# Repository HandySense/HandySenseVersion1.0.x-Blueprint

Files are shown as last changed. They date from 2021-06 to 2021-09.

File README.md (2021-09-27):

hds-logo_0
- 📫 VDO สอนใช้งาน HandySense: ...
[VDO_สอนใช้งาน_HandySense_Link_(คลิกเพื่อดู)](https://www.youtube.com/watch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) 

# HandySense Board 
 

* HandySense คือ ระบบอุปกรณ์ IOT สำหรับเกษตรอัจฉริยะที่สามารถแสดงค่าข้อมูล ปัจจัยในการควบคุมผลผลิตทางการเกษตร โดยใช้เทคโนโลยีเซนเซอร์เข้ามาช่วยในกระบวนการเพาะปลูกซึ่งช่วยให้เกษตรกรสามารถควบคุมสภาวะแวดล้อมในการปลูกได้ตั้งแต่เริ่มต้นส่งผลให้สามารถควบคุมคุณภาพและประเมินปริมาณผลผลิต 
* รวมถึงช่วยเรื่องการเพิ่มคุณค่าของผลผลิตได้โดยใช้การควบคุมกระบวนการเพาะปลูกเพื่อให้ผลผลิตออกในช่วงที่มีความต้องการหรือผลผลิตขาดแคลนรวมถึงการช่วยเกษตรกรนำองค์ความรู้ที่เกิดจากทักษะที่ไม่สามารถถ่ายทอดให้เข้าใจได้เนื่องจากเป็นภูมิปัญญาและเป็นการทำเกษตรกรรมแบบวิถีชาวบ้านโดยการลองผิดลองถูกหรือเป็นองค์ความรู้ที่สืบทอดต่อกัน
 
สารบัญ (Table of contents)
=========================

<!--ts-->
   * [Descriptions](#descriptions)
     องค์ประกอบของบอร์ด HandySense 
   * [Schematic](#schematic)
     ไฟล์ .brd (PCB  layout) และ .sch
   * [Blueprint](#blueprint)
     (GerberFile)
   * [BOM](#bom)
     รายการอุปกรณ์อิเล็กทรอนิกส์ BOM (bill of material)
   * [Manual](#manual)
     คู่มือการใช้งาน 
<!--te-->

Descriptions
===========
### องค์ประกอบของบอร์ด-HandySense 

โดย HandySense Board ประกอบด้วยอินเตอร์เฟสการสื่อสารหลักเป็น I2C, SPI, Analog, WIFI 
* I2C ต่อ Connector ออกมาให้ใช้งาน 2 ชุด (+5V)  
* Analog ต่อ Connector ออกมาให้ใช้งาน 3 pin ได้แก่ IO36(A0), IO39(A3), IO32(A4)
* SPI ขา CS/SS เป็น IO5 บนบอร์ดไม่ได้ต่ออุปกรณ์ แต่ต่อกับ IDC10 (block 10 pin) 
* ส่วน WIFI สื่อสารข้อมูลกับ Server เป็นหลัก
* Output เป็น Relay 220V AC 10A โดยต่อ pin ได้แก่ IO25, IO4, IO12, IO13 

* รายละเอียดแสดงดังภาพ (*แสดงพอสังเขป โดยรายละเอียดอ่านคู่มือเพิ่มเติม)

hds-pinio

Schematic
===========
### ไฟล์ .brd (PCB  layout) และ .sch
สำหรับ HandySense version นี้ออกแบบด้วยโปรแกรม Autodesk Eagle ซึ่งไฟล์สามารถกดดาวน์โหลดได้ด้านบน 

* ไฟล์ .brd (PCB  layout) และ .sch
sch

Blueprint
===========
### Gerber File
สำหรับ BluePrint จะ save เป็น Gerber File ที่สามารถนำไปสั่งผลิตได้ โดยไม่ต้องปรับแก้อะไร สามารถดาวน์โหลดได้ด้านบน

* Gerber File 
gerber

BOM
===========
### รายการอุปกรณ์อิเล็กทรอนิกส์ BOM (Bill Of Material)
* สำหรับรายการอุปกรณ์อิเล็กทรอนิกส์ของบอร์ด HandySense มีรายการทั้งหมดอยู่ในไฟล์ ชื่อ HandySense_v1.0.2_BOM.ods (เปิดดูด้วยโปรแกรม MS Excel)
ซึ่งจะบอกรายละเอียดที่จำเป็นและราคาต่อบอร์ดหรือราคารวมคร่าว ๆ ได้ (อาจจะมี +,- เนื่องจากราคามีการอับเดตเป็นช่วง ๆ ขึ้นอยู่กับผู้ขาย) สามารถที่จะระบุจำนวนบอร์ดที่ต้องการได้ในช่อง

* BOM (Bill Of Material)
bom

Manual
===========
### คู่มือการใช้งาน 
* สำหรับคู่มือการใช้งาน จะประกอบไปด้วย 2 เล่ม ได้แก่ 
* คู่มือสอนใช้งานบอร์ด HandySense
* คู่มือสอนใช้งาน HandySense Dashboard 

bom

# Open Hardware Facts
ost

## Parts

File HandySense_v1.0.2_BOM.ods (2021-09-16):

Handy Sense version 1.0.2
คำอธิบาย : - Product P/N คือหมายเลขที่สามารถนำไปสั่งซื้อผ่านทางร้านได้โดยตรงและง่ายขึ้น - Unit/Board แสดงจำนวนอุปกรณ์ต่อ 1 บอร์ด - Unit/Boards แสดงจำนวอุปกรณ์ต่อจำนวนบอร์ดที่ต้องการผลิต
จำนวนบอร์ดที่ต้องการผลิต |  | 10 | บอร์ด
 |  | * หมายเหตุ ระบุจำนวนที่ต้องการผลิตในช่อง
Part | Value | Device | Package | Product P/N: | ES P/N: | Unit/Board | Unit/Boards | Vendor | ของเหลือ | ซื้อเพิ่ม | ราคา/หน่วย | ราคาต่อ/จำนวนบอร์ดที่ต้องการ
C1,C2,C4 | 10uF | 10UF-16V-10%(TANT) | EIA3216 | TCA1C106M8R | 0176-0142-4 | 3 | 30 | ES | 14 | 16 | 2.5 | 40.00
C6 | 100uF | CAP_POL7343 | EIA7343 | TAJD107K016RNJ | 0092-0305-6 | 1 | 10 | ES | 5 | 5 | 12.86 | 64.30
C3,5,7-12 | 0.1uF | CAP0805 | 805 | CL21B104KBCNNNC | 0082-0192-3 | 5 | 50 | ES | 50 | 0 | 0.42 | 0.00
D1,D2,D3 |  | DIODE-SCHOTTKY-MBRA140 | SMA-DIODE | RB168L-40TE25 | 0176-0726-8 | 3 | 30 | ES | 3 | 27 | 2.79 | 75.33
Ju1 | Female Header | Female Header 6 Pins,Single Row | FHSS06G10 | - | 0007-1218-3 | 1 | 10 | ES | 5 | 5 | 4.31 | 21.55
USB | MICRO_USB_B_HIROSE_ZX62-B-5PA(11) | MICRO_USB_B_HIROSE_ZX62-B-5PA(11) | USB_MICRO_B-HIROSE-ZX62-B-5PA(11) | MRUMRB05FTKTY-30U | 0007-1315-9 | 1 | 10 | ES | 0 | 10 | 20.65 | 206.50
K1-4 | JS-M1-9V-4 | JS-M1-9V-4 | JS-M | HRS4H-S-DC5V-C | 0181-0027-9 | 4 | 40 | ES | 0 | 40 | 19.71 | 788.40
LED1,2 | BLUE | LEDCHIPLED_BLUE | CHIPLED_0805 | TO-2013BC-BF | 0010-1475-9 | 1 | 10 | ES | 14 | 0 | 2.26 | 0.00
LED9,11,13,15 | Green | LEDCHIPLED_GREEN | CHIPLED_0805 | TO-2013BC-MGE | 0010-0326-9 | 4 | 40 | ES | 0 | 40 | 1.54 | 61.60
LED3 | RED | LEDCHIPLED_RED | CHIPLED_0805 | TO-2013BC-MRE | 0010-0327-2 | 2 | 20 | ES | 20 | 0 | 1.54 | 0.00
LED7 | Yellow | LEDCHIPLED_YELLOW | CHIPLED_0805 | TO-2013BC-MYE | 0010-1457-5 | 1 | 10 | ES | 12 | 0 | 1.31 | 0.00
OK1-4 | PC817 | PC817 | DIL04 | PC817X3NSZ9F | 0084-0059-3 | 4 | 40 | ES | 40 | 0 | 3.16 | 0.00
Q1-6 | MMBT2222A | TRANSISTOR_NPNMMBT2222A | SOT23-3 | MMBT2222ALT1G | 0235-0237-0 | 6 | 60 | ES | 0 | 60 | 0.74 | 44.40
R1-4,7,8,14,16,19,22,25,39-50 | 10k | R-US_R0805 | R0805 | MCR10ERTJ103 | 0176-0924-2 | 8 | 80 | ES | 0 | 80 | 0.15 | 12.00
R5,6,9,10,15,17-21,23-26 | 1k | R-US_R0805 | R0805 | MCR10EZPJ102 | 0176-1715-9 | 16 | 160 | ES | 0 | 160 | 0.15 | 24.00
SW0,SW1,SW2 | TACTILE-SWITCH-PTH | TACTILE-SWITCH-PTH | TAC-SWITCH-PTH | TC-0104-X-ROHS | 0171-0104-9 | 3 | 30 | ES | 0 | 30 | 1.49 | 44.70
LDO | LDO Voltage Regulator,3.3V | V_REG_LM1117SOT223 | SOT223 | LM1117MPX-3.3/NOPB | 0078-0169-8 | 1 | 10 | ES | 0 | 10 | 15.11 | 151.10
X1 | ESP-32 | ESP-32 | ESP-32 | ESP32-WROOM-32 | 1082-0002-1 | 1 | 10 | ES | 0 | 10 | 130.5 | 1,305.00
X7,10 | Screw Terminal Block 4Pins,Pitch 5.00mm | W237-04P | W237-4P | ED500V-04P | 0005-0111-7 | 3 | 30 | ES | 30 | 0 | 12.95 | 0.00
X2,6,8,12 | Screw Terminal Block 3Pins,Pitch 5.00mm | W237-03P | W237-133 | EK500V-3P | 0005-0067-0 | 4 | 40 | ES | 20 | 20 | 11.02 | 220.40
X4,5,11 | Screw Terminal Block 3Pins,Pitch 5.00mm | - | - | DG126-03P-14-00A(H) | 0330-0049-4 | 3 | 30 | ES | 20 | 10 | 3.28 | 32.80
IDC10 | BOX Header Connector 10 Pins | BOX Header Connector 10 Pins Dual Row Pitch 2.54 mm | PAK100/2500-10 | SCP10GS31/RH | 0007-0455-4 | 1 | 10 | ES | 3 | 7 | 2.88 | 20.16
Q9 | 32.768kHZ | CRYSTALTC26H | TC26H | Q11C02RX1002200 | 0057-0038-2 | 1 | 10 | ES | 0 | 10 | 2.9 | 29.00
U2 | CP2102N-A01-GQFN28 | CP2102N-A01-GQFN28 | QFN50P500X500X80-29N | IC Usb To Uart |  | 1 | 10 | RS | 0 | 10 | 44.02 | 440.20
BT1 | Battery Holder for CR-2025 | BATTERY-20MM_PTH_KIT | BATTCOM_20MM_PTH_KIT | BH-25T-GLD | 0197-0001-3 | 1 | 10 | ES | 5 | 5 | 4.86 | 24.30
BT2 | 3V/225mAh, Diameter 20 mm | Lithium Coin Battery 3V/225mAh, Diameter 20 mm | BATTCOM_20MM_PTH_KIT | CR-2032L/BE | 0102-0020-1 | 1 | 10 | ES | 0 | 10 | 9.28 | 92.80
U3 | DS1307Z | DS1307Z | SO08-0.15 | Maxim DS1307 | 0067-0085-4 | 1 | 10 | ES | 5 | 5 | 21.16 | 105.80
R4 | 47.5k | R-US_R0805 | R0805 | MCR03EZPFX4702 | 0176-2036-4 | 1 | 10 | ES | 30 | 0 | 0.11 | 0.00
R6 | 2k | R-US_R0805 | R0805 | 0805W8F2001T5E | 0150-2037-4 | 1 | 10 | ES | 40 | 0 | 0.1 | 0.00
R22 | 22.1k | Thick Fillm Chip Resistors 1/4W | 223 | MCR18EZHJ223 | 0176-1928-6 | 1 | 10 | ES | 30 | 0 | 0.17 | 0.00
R4.7 | 4.7K |  |  |  | 0150-1882-3 | 3 | 30 | ES | 30 | 0 | 0.11 | 0.00
H1-2 | 2 pin | Water 2 Pins, Pitch 2.54 mm | Connector | 600102ST | 0007-1119-1 | 2 | 2 | ES | 2 | 0 | 0 | 0.00
CA1-6 | TVS Diode 600W,Breakdown Voltage 11.7V(Typ.) |  |  | VS8V0UA1LAMTR | 0176-1511-3 | 4 | 40 | ES | 0 | 40 | 19.81 | 792.40
MF1-2 | MF-MSMF110/24X-2 | Bourns 1.1A Surface Mount Resettable Fuse, 24V |  |  |  | 2 | 20 | RS | 0 | 20 | 5.53 | 110.60
 |  |  |  |  |  |  |  |  |  | 0
 |  |  |  |  |  |  |  |  |  |  | รวม | 4,707.34

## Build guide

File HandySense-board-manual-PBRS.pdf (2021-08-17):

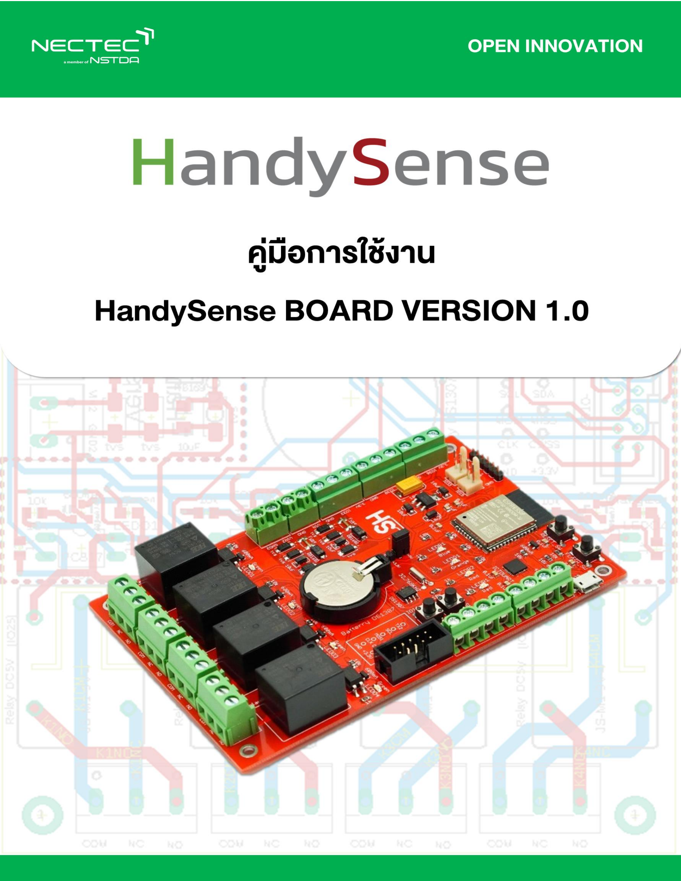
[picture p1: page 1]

คู่มือการใช้งานบอร์ด HandySense | ก

## สารบัญ

เรื่อง | หน้า

### 1. ดาวน์โหลดและติดตั้งโปรแกรม

1.1 วิธีดาวน์โหลดโปรแกรม Arduino IDE | 1
1.2 วิธีติดตั้งโปรแกรม Arduino IDE | 2
1.3 วิธีติดตั้งไมโครคอนโทรลเลอร์ ESP32 ในโปรแกรม Arduino IDE | 6

### 2. บอร์ด HandySense VERSION 1.0

2.1 ส่วนประกอบของบอร์ด HandySense VERSION 1.0 | 8
2.2 บอร์ดลายวงจรที่ประกอบแล้ว (Assembled PCB) | 9
2.3 ลายแผนผังวงจร | 10
2.4 PCB เลเอาท์ | 11

### 3. เริ่มต้นใช้งานบอร์ด HandySense VERSION 1.0

3.1 เชื่อมต่อบอร์ด HandySense VERSION 1.0 กับเซนเซอร์ (Sensor) | 12
3.1.1 คอนเน็กเตอร์พินรับค่าอนาล็อก, ดิจิทัล (I/O) และ I2C | 12
3.2 เชื่อมต่อบอร์ด HandySense VERSION 1.0 กับอุปกรณ์สั่งการ (Actuator) | 14
3.2.1 คอนเน็กเตอร์พินสั่งการท างาน (I/O) | 14
3.2.2 ภาพรวมการเชื่อมต่อของระบบเซนเซอร์และอุปกรณ์สั่งการ | 14
3.3 ฟังก์ชันการท างานของบอร์ด HandySense VERSION 1.0 | 15

### 4. ใช้งานเฟิร์มแวร์ (Firmware) ของบอร์ด HandySense VERSION 1.0

4.1 วิธีดาวน์โหลดเฟิร์มแวร์ (Firmware) | 16
4.2 ติดตั้งไลบรารี่ (Library) ของเฟิร์มแวร์ (Firmware) | 17

### 5. ใช้งานเฟิร์มแวร์ (Firmware) ของบอร์ด HandySense VERSION 1.0 ร่วมกับเว็บแอปพลิเคชัน

HandySense
5.1 วิธีเชื่อมต่อกับเว็บแอปพลิเคชัน HandySense | 19
5.1.1 วิธีเพิ่มบอร์ด HandySense VERSION 1.0 บนเว็บแอปพลิเคชัน HandySense | 19

คู่มือการใช้งานบอร์ด HandySense | ข

## สารบัญรูป

เรื่อง | หน้า
รูปที่ 1.0 ขั้นตอนดาวน์โหลด Arduino IDE | 1
รูปที่ 1.1 ดาวน์โหลด Arduino IDE | 2
รูปที่ 1.2 ไอคอนโปรแกรม Arduino IDE | 2
รูปที่ 2.1 ส่วนประกอบหลักของบอร์ด HandySense VERSION 1.0 | 8
รูปที่ 2.2 สคีแมททิคบอร์ดแสดงขาคอนเน็กเตอร์ | 9
รูปที่ 2.3 แผนผังวงจร | 10
รูปที่ 2.4 PCB เลเอาท์ | 11
รูปที่ 3.0 สายเซนเซอร์ | 12
รูปที่ 3.1 ต่อสายเซนเซอร์กับบอร์ด | 13
รูปที่ 3.2 แนะน าต่อสายไฟของอุปกรณ์ที่ต้องการสั่งการกับบอร์ด | 14
รูปที่ 3.3 ภาพรวมการต่อเชื่อมของอุปกรณ์ | 14
รูปที่ 3.4 แสดงฟังก์ชันการท างานของบอร์ด HandySense VERSION 1.0 | 15
รูปที่ 4.0 คิวอาร์โค้ดขอพิมพ์เขียวและเฟิร์มแวร์ | 16
รูปที่ 4.1 เข้าสู่การดาวน์โหลดเฟิร์มแวร์ | 16
รูปที่ 4.2 ฟอร์มลงทะเบียน | 17

คู่มือการใช้งานบอร์ด HandySense | 1

### 1. ดาวน์โหลดและติดตั้งโปรแกรม

การดาวน์โหลดและติดตั้งโปรแกรมในคู่มือฉบับนี้ เป็นการแนะน าการใช้โปรแกรม Arduino IDE ของ Arduino โดยตรง เพื่อให้สะดวกต่อการเขียนโค้ดและแก้ไขปัญหาต่าง ๆ โดยมีขั้นตอนดังนี้

### 1.1 วิธีดาวน์โปรแกรม Arduino IDE

วิธีการดาวน์โหลดโปรแกรม Arduino IDE สามารถเข้าผ่านเว็บไซต์ของ Arduino ผ่านลิงก์URL : www.arduino.cc/en/software หรือค้นหาใน Google ค าว ่า “Arduino IDE” ให้ดาวน์โหลด เวอร์ชั่นล่าสุด แสดงดังขั้นตอนรูปดังนี้

รูปที่ 1.0 ขั้นตอนดาวน์โหลด Arduino IDE

- ขั้นตอนที่ 1 ให้เลือกหัวข้อ “SOFTWARE”
- ขั้นตอนที่ 2 ให้เลือกโปรแกรม Arduino IDE ให้เหมาะสมกับระบบปฏิบัติการของคอมพิวเตอร์ หรือโน้ตบุ๊กของตัวเอง

1

คู่มือการใช้งานบอร์ด HandySense | 2

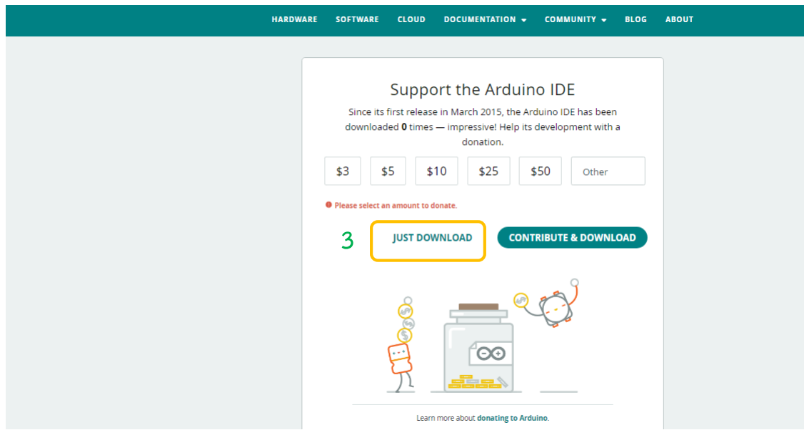
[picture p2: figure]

รูปที่ 1.1 ดาวน์โหลด Arduino IDE
- ขั้นตอนที่ 3 หลังจากกดเลือกโปรแกรม Arduino IDE ให้เหมาะสมกับระบบปฏิบัติการของ คอมพิวเตอร์หรือโน้ตบุ๊กของตัวเองจะปรากฏหน้าต ่างแสดงดังรูปที ่1.1 ให้กดเลือก “JUST DOWNLOAD” คอมพิวเตอร์หรือโน้ตบุ๊กจะดาวน์โหลดโปรแกรมให้อัตโนมัติ

### 1.2 วิธีติดตั้งโปรแกรม Arduino IDE

หลังจากดาวน์โหลดไปแล้วให้ไปยังโฟลเดอร์ที่ดาวน์โหลดเพื่อเริ่มการติดตั้งโปรแกรม Arduino IDE ลงในคอมพิวเตอร์หรือโน้ตบุ๊ก แสดงขั้นตอนดังรูป

รูปที่ 1.2 ไอคอนโปรแกรม Arduino IDE

- ขั้นตอนที่ 4 ดับเบิ้ลคลิกที่ไอคอนโปรแกรมเพื่อเริ่มการติดตั้งโปรแกรม Arduino IDE (ขั้นตอน การติดตั้งที่แสดงนี้เป็นการติดตั้งบนระบบปฏิบัติการวินโดวส์ “Windows”)

คู่มือการใช้งานบอร์ด HandySense | 3

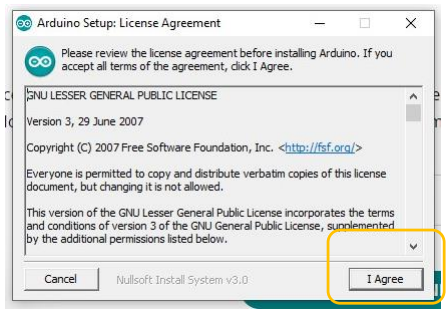
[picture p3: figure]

- ขั้นตอนที่ 5 หลักจากนั้นให้กด “I Agree” เพื่อเข้าสู่การติดตั้งในกระบวนการต่อไป
- ขั้นตอนที่ 6 ในการเลือก “Components” แนะน าให้เลือกทั้งหมดแล้วให้กด “Next” เพื่อ เข้าสู่การติดตั้งในกระบวนการต่อไป

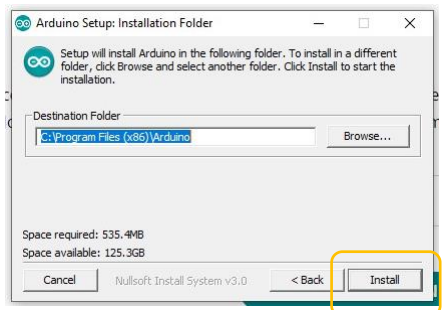
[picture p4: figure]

- ขั้นตอนที่ 7 ให้กด “Install” เพื่อเข้าสู่การติดตั้งในกระบวนการต่อไป

คู่มือการใช้งานบอร์ด HandySense | 4

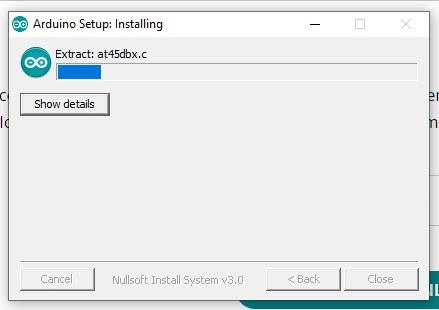
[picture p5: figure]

- ขั้นตอนที่ 8 หลังจากกด “Install” โปรแกรมจะท าการติดตั้ง ตรงนี้ให้รอจนกว่าสีฟ้าจะวิ่งเต็ม ช่อง

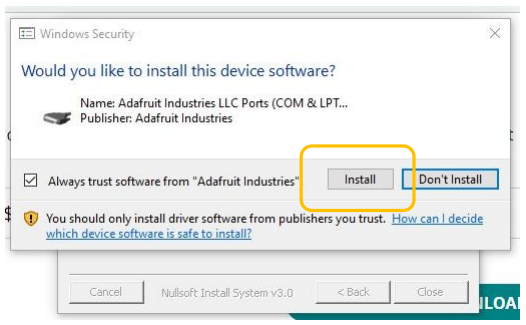
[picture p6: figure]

- ขั้นตอนที่ 9 หากเป็นการติดตั้งครั้งแรกบนระบบปฏิบัติการวินโดวส์จะเกิดการแจ้งเตือนเกิดขึ้น ให้กด “Install”

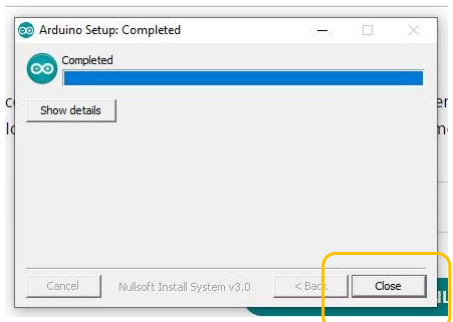
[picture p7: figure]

- ขั้นตอนที่ 10 เมื่อช่องสีฟ้าเต็มช่อง แสดงถึงกระบวนการติดตั้งเสร็จสิ้นให้กด “Close”

คู่มือการใช้งานบอร์ด HandySense | 5

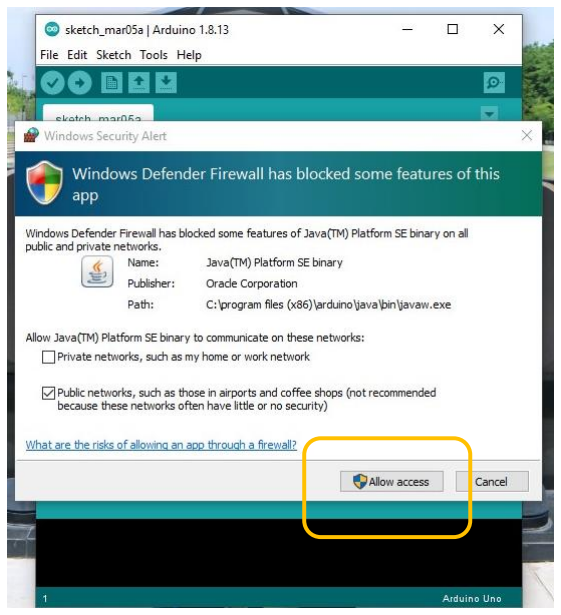
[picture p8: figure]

- ขั้นตอนที่ 11 หลังจากนั้นบนหน้า Desktop ของคอมพิวเตอร์หรือโน้ตบุ๊กจะมีไอคอนของ โปรแกรม Arduino IDE เพิ่มขึ้นมาให้ดับเบิ้ลคลิกที่ไอคอนโปรแกรมเพื่อเปิดโปรแกรมขึ้น หากเปิดใช้งาน ครั้งแรกจะมีหน้าแสดงดังรูปให้กด “Allow access” เพื่ออนุญาตการเปิดใช้งานโปรแกรม
- ขั้นตอนที่ 12 หลังจากติดตั้งโปรแกรม Arduino IDE เสร็จให้เปิดโปรแกรมขึ้นมาจะแสดงดังรูป เพื่อทดสอบการเขียนโค้ดหรือน าโค้ดตัวอย่างมาทดสอบ หากท างานได้ปกติเป็นอันเสร็จสิ้นสมบูรณ์

คู่มือการใช้งานบอร์ด HandySense | 6

### 1.3 วิธีติดตั้งไมโครคอนโทรลเลอร์ ESP32 ในโปรแกรม Arduino IDE

ขั้นตอนนี้จะเป็นขั้นตอนที่ส าคัญที่สุดในการใช้ ESP32 เนื่องจากเป็นการลงไดรเวอร์ของตัว ESP32 ใน โปรแกรม Arduino IDE เพื่อให้สามารถเบิร์นโค้ดโปรแกรมลงบอร์ดได้ โดยมีขั้นตอนการติดตั้งดังนี้

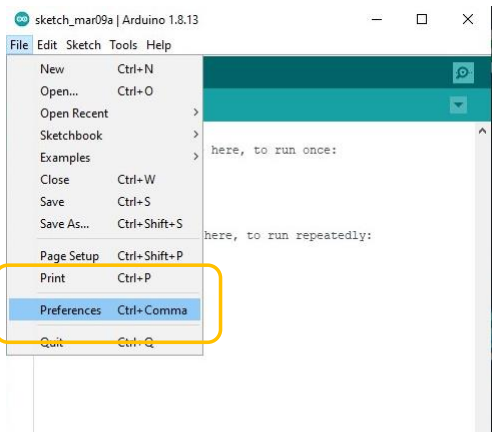
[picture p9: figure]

- ขั้นตอนที่ 1 เปิดโปรแกรมแล้วเข้าไปที่ “File > Preferences”
- ขั้นตอนที่ 2 คัดลอกลิงก์https://dl.espressif.com/dl/package_esp32_index.json แล้วน าไปวาง เพิ่มในช่องดังรูป จากนั้นกดปุ่ม “OK”

คู่มือการใช้งานบอร์ด HandySense | 7

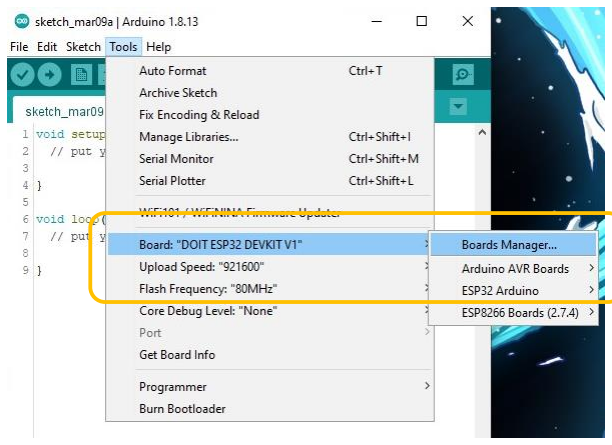
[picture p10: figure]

- ขั้นตอนที่ 3 เข้าไปที่ “Tool > Board: > Board > Boards Manager”
- ขั้นตอนที่ 4 หลังจากนั้นหน้าจอจะปรากฏดังรูปให้กดค้นหาค าว่า “esp32” และท าการติดตตั้ง

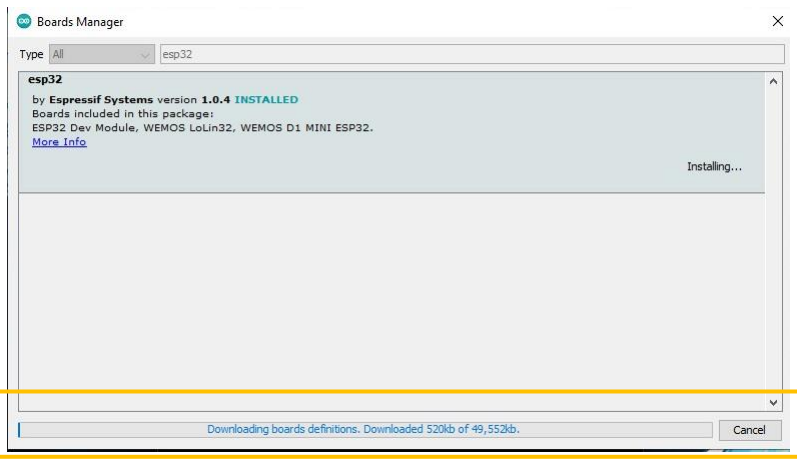
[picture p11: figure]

- ขั้นตอนที่5 รอการดาวน์โหลด หากช่องสีฟ้าเต็ม หมายถึงการติดตั้งเสร็จสมบูรณ์

คู่มือการใช้งานบอร์ด HandySense | 8

### 2. บอร์ด HandySense VERSION 1.0

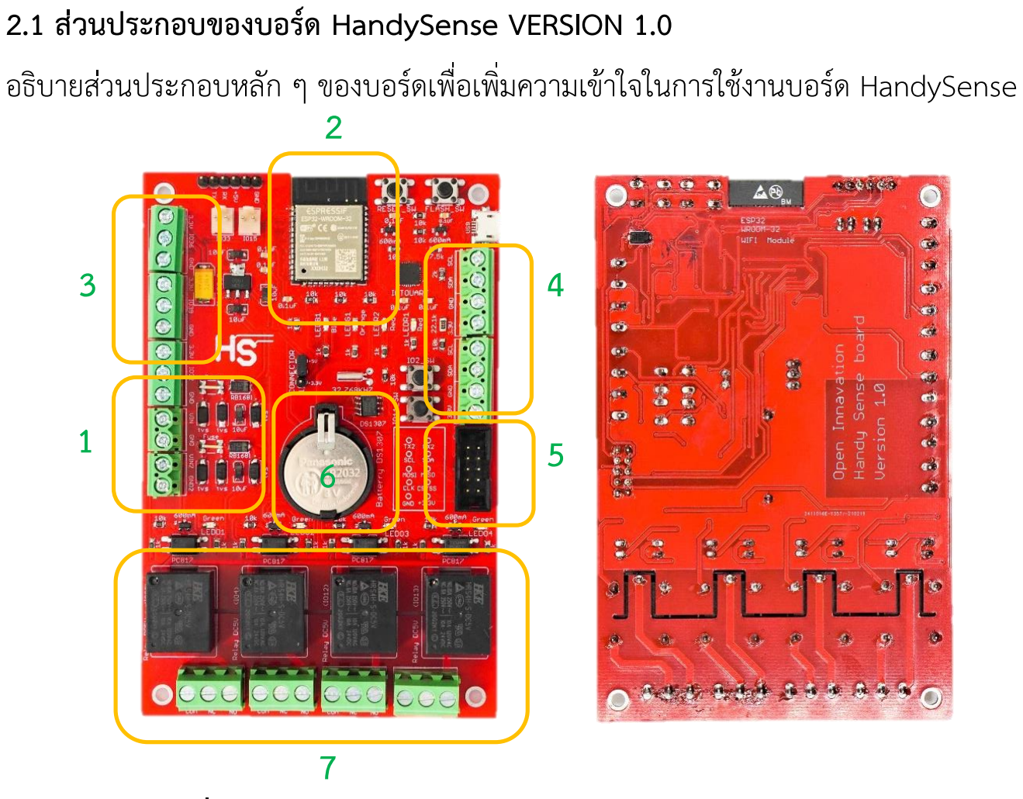
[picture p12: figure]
2.1 ส่วนประกอบของบอร์ด HandySense VERSION 1.0 อธิบายส่วนประกอบหลัก ๆ ของบอร์ดเพื่อเพิ่มความเข้าใจในการใช้งานบอร์ด HandySense 2

รูปที่ 2.1 ส่วนประกอบหลักของบอร์ด HandySense VERSION 1.0

1. คอนเน็กเตอร์ส าหรับต ่อไฟเลี้ยง (V INPUT) 5V DC เพื ่อเลี้ยงไฟให้กับบอร์ด HandySense VERSION 1.0
2. คอนโทรลเลอร์ (Controller) ESP32 ส าหรับเขียนโค้ดโปรแกรมและเชื่อมต่อไวไฟ (WIFI)
3. คอนเน็กเตอร์พินอินพุต (INPUT PIN) ส าหรับอ่านค่าเซนเซอร์แบบอนาล็อกหรือดิจิทัลที่มีค่าแรงดัน สัญญาณขาเข้าไม่เกิน 3V3 โวลต์
4. คอนเน็กเตอร์พินอินพุต (INPUT PIN) ส าหรับอ่านค่าเซนเซอร์แบบ I2C มีไฟเลี้ยงไม่เกิน 3V3 โวลต์
5. คอนเน็กเตอร์แบบ IDC10 ส าหรับต่อเซนเซอร์หรือโมดูลที่มีรูปแบบการสื่อสารแบบ UART, SPI แยก เป็นส่วนเสริมออกจากบอร์ดหลัก
6. RTC (Real Time Clock) ส าหรับการนับเวลา เมื่อต้องการใช้เวลามาช่วยในการเขียนโค้ด
7. คอนเน็กเตอร์พินเอ้าท์พุต (OUTPUT PIN) ส าหรับต่อกับอุปกรณ์ที่ต้องควบคุม 4 ช่อง (Channel)

คู่มือการใช้งานบอร์ด HandySense | 9

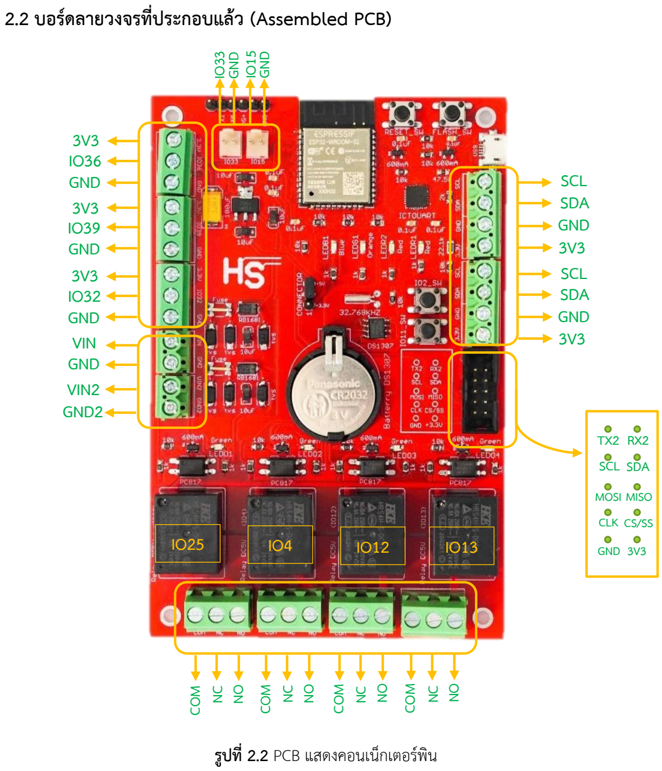
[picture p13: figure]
2.2 บอร์ดลายวงจรที่ประกอบแล้ว (Assembled PCB); รูปที่ 2.2 PCB แสดงคอนเน็กเตอร์พิน; 3V3 IO36 GND 3V3 IO39 GND 3V3 IO32 GND VIN GND VIN2 GND2; IO33 GND; IO15 GND; COM; SCL SDA GND 3V3 SCL SDA; GND; TX2 RX2 SCL SDA; MOSI MISO CLK CS/SS; GND 3V3 IO25

สคีแมททิคบอร์ดแสดงคอนเน็กเตอร์พินส าหรับการเชื่อมต่อเซนเซอร์และอุปกรณ์ที่ต้องการควบคุมสั่งการ ท างานนั้นมีคอนเน็กเตอร์พิน ดังนี้
1. คอนเน็กเตอร์พิน INPUT เซ็นเซอร์ประกอบด้วย I/O32, I/O36, I/O39, I/O15, I/O33
2. คอนเน็กเตอร์พิน OUTPUT แสดงสถานะการท างานต่าง ๆ ของบอร์ด HandySense เมื่อต้องการ แสดงหน้ากล่องควบคุม ประกอบด้วย I/O15, I/O33
3. คอนเน็กเตอร์พินต่อเซ็นเซอร์ I2C

คู่มือการใช้งานบอร์ด HandySense | 10
4. คอนเน็กเตอร์IDC10 INPUT UART, SPI, I2C โมดูล
5. คอนเน็กเตอร์พิน OUTPUT ควบคุมอุปกรณ์ ประกอบด้วย I/O25, I/O4, I/O12, I/O13

### 2.3 วงจรสคีแมททิค (Schematic diagram) แผนผังวงจร

รูปที่ 2.3 แผนผังวงจร

คู่มือการใช้งานบอร์ด HandySense | 11

### 2.4 PCB เลเอาท์

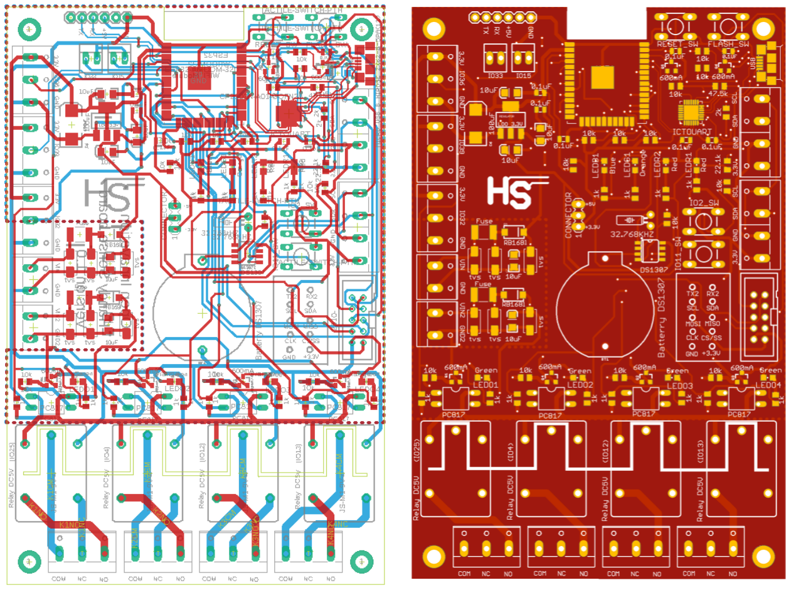
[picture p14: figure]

รูปที่ 2.4 PCB เลเอาท์

วงจรสคีแมททิค (Schematic), PCB เลเอาท์และไฟล์ GB-file ส าหรับสั่งท าแผ่นวงจร PCB สามารถเข้า ไปลงทะเบียนทางเว็บไซต์ HandySense Information เพื่อขอไฟล์และเอกสารต่าง ๆ โดยมีรูปแบบเป็น Open sourceและในเว็บไซต์ยังรวมข้อมูลข่าวสารต่าง ๆ งานวิจัยระบบ HandySenseและผลงานอื่น ๆ ให้ได้ศึกษา และ ความเข้าใจน าไปประยุกต์ใช้อีกด้วย

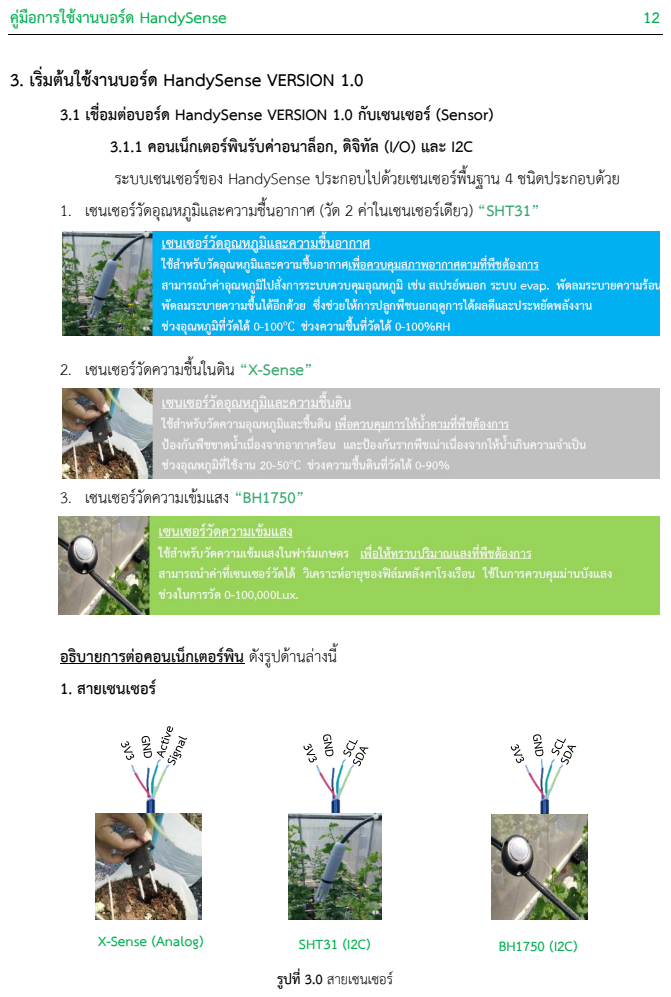
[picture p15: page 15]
คู่มือการใช้งานบอร์ด HandySense; X-Sense (Analog); SHT31 (I2C); รูปที่ 3.0 สายเซนเซอร์

3. เริ่มต้นใช้งานบอร์ด HandySense VERSION 1.0
3.1 เชื่อมต่อบอร์ด HandySense VERSION 1.0 กับเซนเซอร์ (Sensor)
3.1.1 คอนเน็กเตอร์พินรับค่าอนาล็อก, ดิจิทัล (I/O) และ I2C
ระบบเซนเซอร์ของ HandySense ประกอบไปด้วยเซนเซอร์พื้นฐาน 4 ชนิดประกอบด้วย
1. เซนเซอร์วัดอุณหภูมิและความชื้นอากาศ (วัด 2 ค่าในเซนเซอร์เดียว) “SHT31”

2. เซนเซอร์วัดความชื้นในดิน “X-Sense”

3. เซนเซอร์วัดความเข้มแสง “BH1750”

อธิบายการต่อคอนเน็กเตอร์พิน ดังรูปด้านล่างนี้
1. สายเซนเซอร์

คู่มือการใช้งานบอร์ด HandySense | 13

### 2. เชื่อมต่อสายเซนเซอร์กับบอร์ด

รูปที่ 3.1 ต่อสายเซนเซอร์กับบอร์ด

X-Sense เป็นเซนเซอร์ส าหรับวัดค่าความชื้นในดินในหน่วยเปอร์เซ็นต์(%) โดยหลัก ๆ แล้วจะประกอบ ไปด้วย 4 สายได้แก่ สายไฟเลี้ยง, สายกราวด์, สายสัญญาณและสายแอคทีฟ โดยสายแอคทีฟจะเป็นเหมือนโหมด ในการปิด-เปิด X-Sense เซนเซอร์ เช่น หากต่อสายแอคทีฟเข้ากับไฟเลี้ยง 3V3 เซนเซอร์จะเปิดท างาน หากต่อ สายแอคทีฟลงกราวด์เซนจะไม่วัดค่าต่าง ๆ ดังนั้นเราต้องการเปิดใช้งานตลอดเวลาจึงต่อเข้ากับไฟเลี้ยง 3V3 โวลต์ ส าหรับเซนเซอร์ SHT31, BH1750 ส่วนใหญ่แล้วจะประกอบได้ 4 สายหลัก ๆ ได้แก่ สายไฟเลี้ยง, สาย กราวด์, สาย SCL และสาย SDA สามารถต่อได้แบบตรง ๆ ไม่ได้มีโหมดเหมือน X-Sense

X-Sense (Analog)

SHT31 (I2C)

BH1750 (I2C)

Analog
3V3
GND
Active
Signal

3V3
GND
SDA
SCL

I2C

คู่มือการใช้งานบอร์ด HandySense | 14

### 3.2 เชื่อมต่อบอร์ด HandySense VERSION 1.0 กับอุปกรณ์สั่งการ (Actuator)

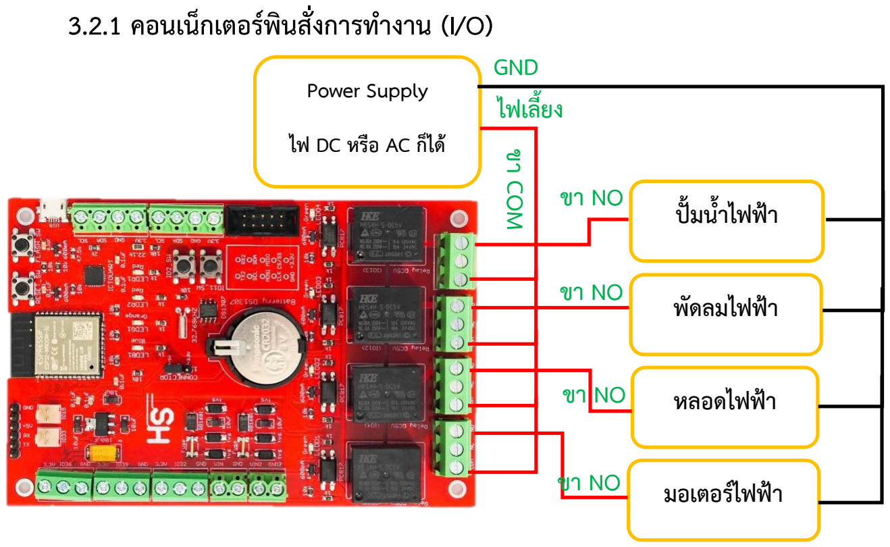
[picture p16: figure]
3.2.1 คอนเน็กเตอร์พินสั่งการท างาน (I/O); Power Supply; ขา COM; ปั้มน้ำไฟฟ้า; พัดลมไฟฟ้า; หลอดไฟฟ้า; มอเตอร์ไฟฟ้า; GND ไฟเลี้ยง

รูปที่ 3.2 แนะน าต่อสายไฟของอุปกรณ์ที่ต้องการสั่งการกับบอร์ด

การต่อสายไฟของอุปกรณ์ที่ต้องการสั่งการท างานเข้ากับบอร์ด HandySense ให้ต่อไฟเลี้ยงเข้า คอนเน็กเตอร์พิน “COM” ก่อนหลังจากนั้นให้ต่อสายไฟอีกหนึ่งเส้นเข้าคอนเน็กเตอร์พิน “NO” ส่วนอีก ด้านให้ต่อไปยังไฟเลี้ยงของอุปกรณ์นั้น ๆ ไป หลังจากนั้นให้ต่อสายกราวด์ของแหล่งจ่ายพลังงาน (Power Supply) เข้ากับกราวด์ของอุปกรณ์นั้น ๆ ด้วย ซึ่งเป็นไปตามรูปด้านบน

### 3.2.2 ภาพรวมการเชื่อมต่อของระบบเซนเซอร์และอุปกรณ์สั่งการ

รูปที่ 3.3 ภาพรวมการต่อเชื่อมของอุปกรณ์

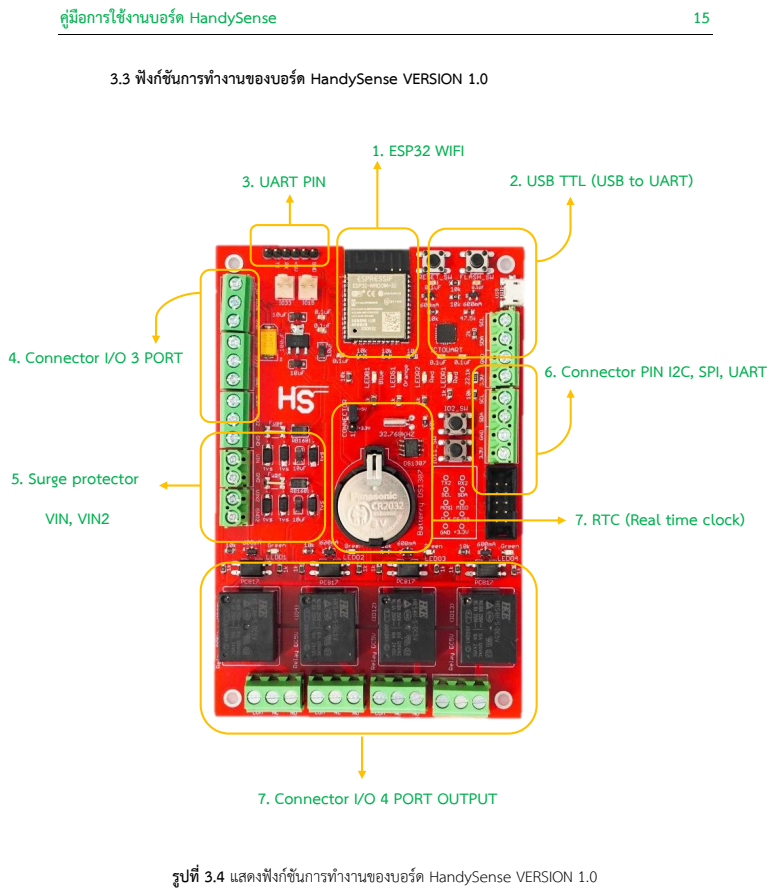
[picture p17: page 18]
คู่มือการใช้งานบอร์ด HandySense; 4. Connector I/O 3 PORT; 3. UART PIN; 1. ESP32 WIFI; 5. Surge protector; VIN, VIN2; 7. RTC (Real time clock)

3.3 ฟังก์ชันการท างานของบอร์ด HandySense VERSION 1.0

2. USB TTL (USB to UART)

6. Connector PIN I2C, SPI, UART

7. Connector I/O 4 PORT OUTPUT

รูปที่ 3.4 แสดงฟังก์ชันการท างานของบอร์ด HandySense VERSION 1.0

คู่มือการใช้งานบอร์ด HandySense | 16

### 4. ใช้งานเฟิร์มแวร์ (Firmware) ของบอร์ด HandySense VERSION 1.0

### 4.1 วิธีดาวน์โหลดเฟิร์มแวร์ (Firmware) และใช้งาน

การดาวน์โหลดเฟิร์มแวร์ของบอร์ด HandySense VERSION 1.0 สามารถดาวน์โหลดได้ฟรี ผ ่านการลงทะเบียนเพียงไม ่กี ่ขั้นตอนบนเว็บไซต์ HandySense หรือสามารถเข้าถึงช ่องทางการ ลงทะเบียนผ่าน Facebook Group “HandySense Community” โดยแสดงขั้นตอนดังนี้

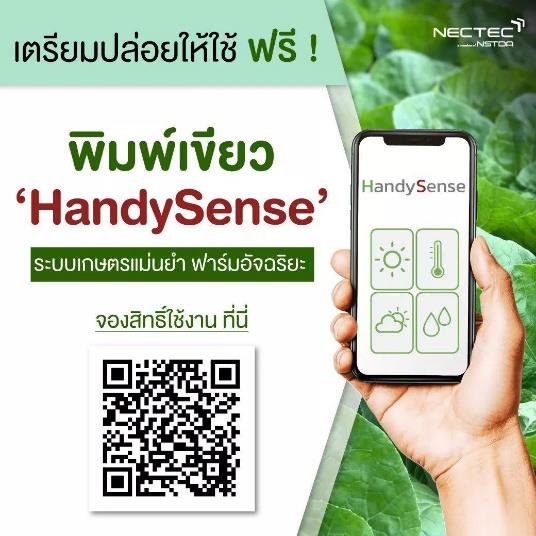
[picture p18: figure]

รูปที่ 4.0 คิวอาร์โค้ดขอพิมพ์เขียวและเฟิร์มแวร์

- ขั้นตอนที่ 1 สแกนคิวอาร์โค้ดจากรูปด้านบน ผ่านมือถือ
- ขั้นตอนที่ 2 หลังจากอ่านบทความเสร็จแล้ว ให้เลื่อนลงมาด้านล่างสุด ให้กด “สนใจเทคโนโลยี”

รูปที่ 4.1 เข้าสู่การดาวน์โหลดเฟิร์มแวร์

คู่มือการใช้งานบอร์ด HandySense | 17

รูปที่ 4.2 ฟอร์มลงทะเบียน
- ขั้นตอนที่ 3 หลังกด “สนใจเทคโนโลยี” จะเข้าสู ่หน้า Google Form โดยจ าเป็นต้องกรอกข้อมูล รายละเอียดต่าง ๆ ให้ถูกต้องและครบถ้วนแล้วกดส่งข้อมูล เนื่องจากหากกรอกข้อมูลเบอร์โทรกับ E-mail ไม่ ถูกต้อง ระบบจะไม่สามารถส่ง Username และ Password เพื่อสู่เว็บไซต์HandySense ได้

### 4.2 ติดตั้งไลบรารี่ (Library) ของเฟิร์มแวร์ (Firmware)

เมื่อได้เฟิร์มแวร์มาแล้วจะต้องท าการดาวน์โหลดไลบรารี่ของเฟิร์มแวร์ก่อน เพื่อให้สามารถเบิร์น เฟิร์มแวร์ให้กับ HandySense VERSION 1.0 ได้ โดยมีขั้นตอนดังนี้

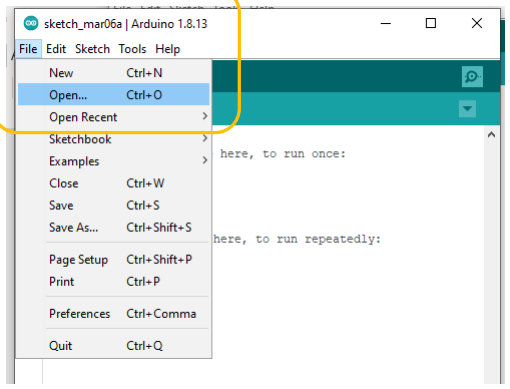
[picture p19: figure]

- ขั้นตอนที่ 1 เริ่มต้นด้วยการเปิดไฟล์เฟิร์มแวร์ โดยไปเลือกที่ “File > Open” ไฟล์เฟิร์มแวร์ที่ได้มา

คู่มือการใช้งานบอร์ด HandySense | 18
- ขั้นตอนที่ 2 หลังจากเปิดไฟล์เฟิร์มแวร์ขึ้นมาแล้วให้เลือกที่ “Sketch > Include Library > Manage Libraries”

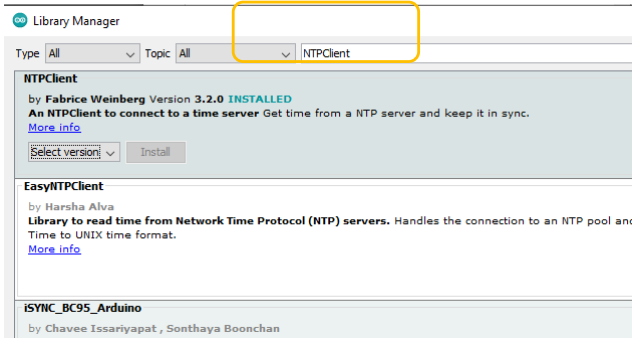
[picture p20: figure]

คู่มือการใช้งานบอร์ด HandySense | 19
- ขั้นตอนที่ 3 หลังจากที่กดแล้วจะมีหน้าต่างขึ้นมาดังรูปโดยการติดตั้งไลบรารี่ให้ป้อนชื่อค้นหาแล้ว กด “Install” ติดตั้งจนครบทุกไลบรารี่ โดยมีไลบรารี่ทั้งหมดที่ต้องติดตั้งดังนี้

เมื่อติดตั้งจนครบแล้ว ให้ทดสอบด้วยการกด “Verify” บนโปรแกรม Arduino IDE หากติดตั้ง ไลบรารี่ครบแล้ว การ Verify จะไม่ติดปัญหาใด ๆ หากติดปัญหาการติดตั้งไลบรารี่เกิดขึ้นให้ลด Version ของไลบรารี่ที่เกิดปัญหานั้น ๆ ลงไป

### 5. ใช้งานเฟิร์มแวร์ (Firmware) ของบอร์ด HandySense VERSION 1.0 ร ่วมก ับเว็บ

แอปพลิเคชัน HandySense

### 5.1 วิธีเชื่อมต่อกับเว็บแอปพลิเคชัน HandySense 5.1.1 วิธีเพิ่มบอร์ด HandySense VERSION 1.0 บนเว็บแอปพลิเคชัน HandySense

หลังจากที่ดาวน์โหลดเฟิร์มแวร์และติดตั้งไลบรารี่จนครบแล้วก็ถึงขั้นตอนของการใช้งานบอร์ด HandySense ร่วมกับเว็บแอปพลิเคชัน HandySense โดยมีขั้นตอนดังนี้

- ขั้นตอนที่ 1 เตรียมสาย USB Type B (Micro-USB), บอร์ด HandySense ให้พร้อมแล้วท าการ เชื่อต่อกับคอมพิวเตอร์หรือโน้ตบุ๊ค

1.Arduino.h
2.WiFi.h
3.Wire.h
4.NTPClient.h
5.PubSubClient.h
6.WiFiUdp.h
7.ArduinoJson.h
8.EEPROM.h
9.Adafruit_SHT31.h

10.BH1750.h
11.RTClib.h
12.time.h
13.WiFiClient.h
14.WebServer.h
15.ESPmDNS.h
16.Update.h
17.StreamUtils.h

คู่มือการใช้งานบอร์ด HandySense | 20
- ขั้นตอนที่ 2 เมื่อท าการเชื่อมต่อแล้ว ให้เลือกรายละเอียดต่าง ๆ ให้เป็นไปตามกรอบสีเหลือง ในส ่วนของ Port “COM3” จะเป็นไปตามคอมพิวเตอร์หรือโน้ตบุ๊กของแต่ละเครื ่อง จากนั้น จึงเบิร์นเฟิร์มแวร์ลงบอร์ด HandySense VERSION 1.0

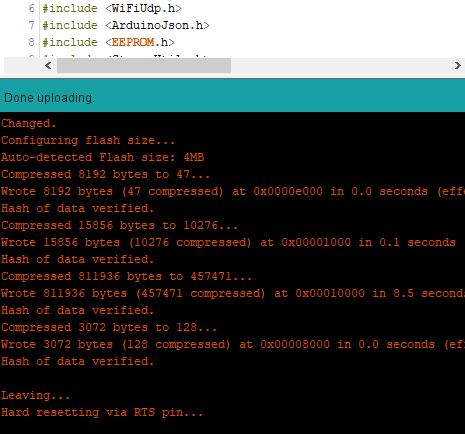
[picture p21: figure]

- ขั้นตอนที่ 3 เมื ่อเบิร์นเฟิร์มแวร์ลง HandySense VERSION 1.0 เสร็จแล้วจะแสดงดังภาพ ด้านบน

คู่มือการใช้งานบอร์ด HandySense | 21
- ขั้นตอนที่4 เปิดเว็บแอปพลิเคชัน HandySenseผ่านลิงก์นี้ : https://auth.netpie.io/login จะแสดงหน้า Login ขึ้นมาหากมี Username และ Password ที ่เป็น Account ของ NETPIE อยู่ก็สามารถเข้าสู่ระบบและใช้งานได้ทันที หรือ กด “Register with NETPIE” เพื่อลงทะเบียน รายละเอียดเพิ่มเติม : สามารถศึกษาจากคู่มือการใช้งานเว็บแอปพลิเคชัน HandySense

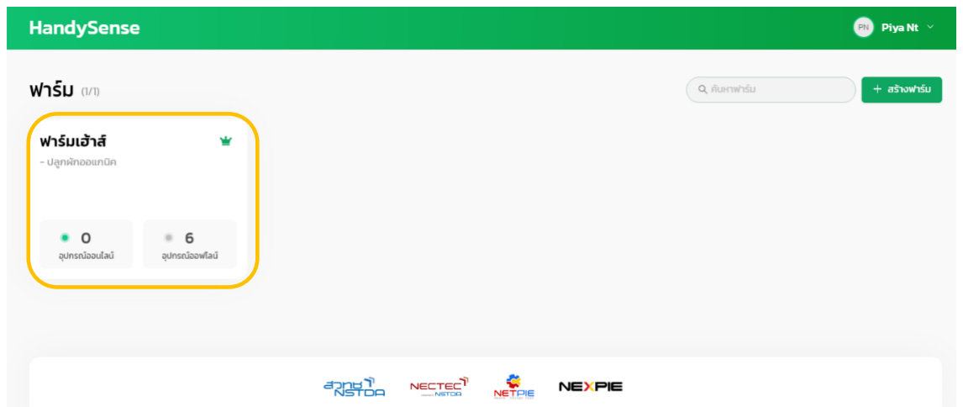
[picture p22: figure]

- ขั้นตอนที่ 5 เข้ามายังหน้าฟาร์มของเราที่ได้สร้างขึ้น กดเข้าสู่เข้าฟาร์มตามกรอบสีเหลือง

คู่มือการใช้งานบอร์ด HandySense | 22
- ขั้นตอนที่ 6 ให้กด “เพิ่มอุปกรณ์” ในขั้นตอนนี้จะต้องเชื่อมต่อสาย USB กับคอมพิวเตอร์หรือโน้ตบุ๊ก จึงจะสามารถท าได้
- ขั้นตอนที่ 7 ให้กด “สร้างอุปกรณ์”
- ขั้นตอนที่ 8 ให้กดเลือก COM Port แล้วกด “Connect”

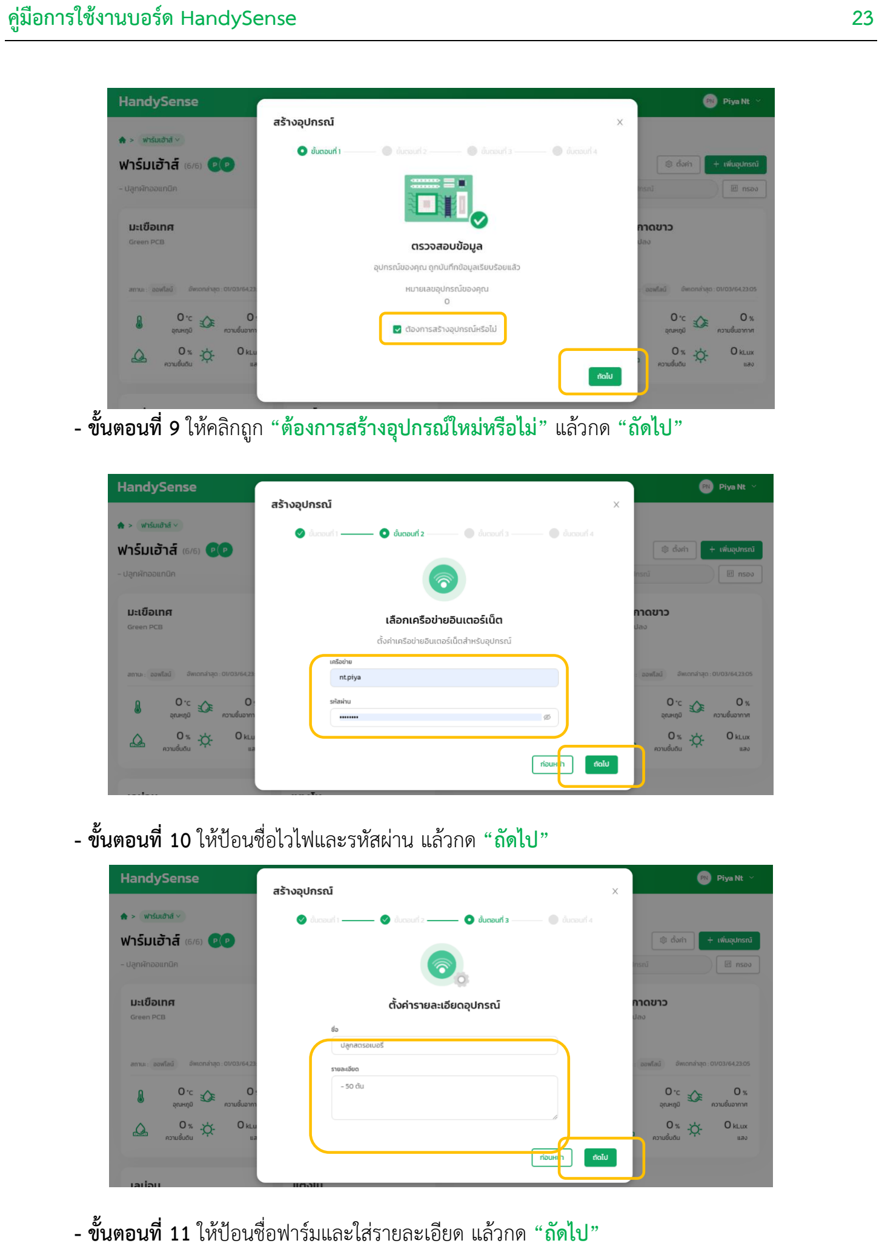
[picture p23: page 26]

คู่มือการใช้งานบอร์ด HandySense | 23
- ขั้นตอนที่9 ให้คลิกถูก “ต้องการสร้างอุปกรณ์ใหม่หรือไม่” แล้วกด “ถัดไป”
- ขั้นตอนที่ 10 ให้ป้อนชื่อไวไฟและรหัสผ่าน แล้วกด “ถัดไป”
- ขั้นตอนที่ 11 ให้ป้อนชื่อฟาร์มและใส่รายละเอียด แล้วกด “ถัดไป”

คู่มือการใช้งานบอร์ด HandySense | 24

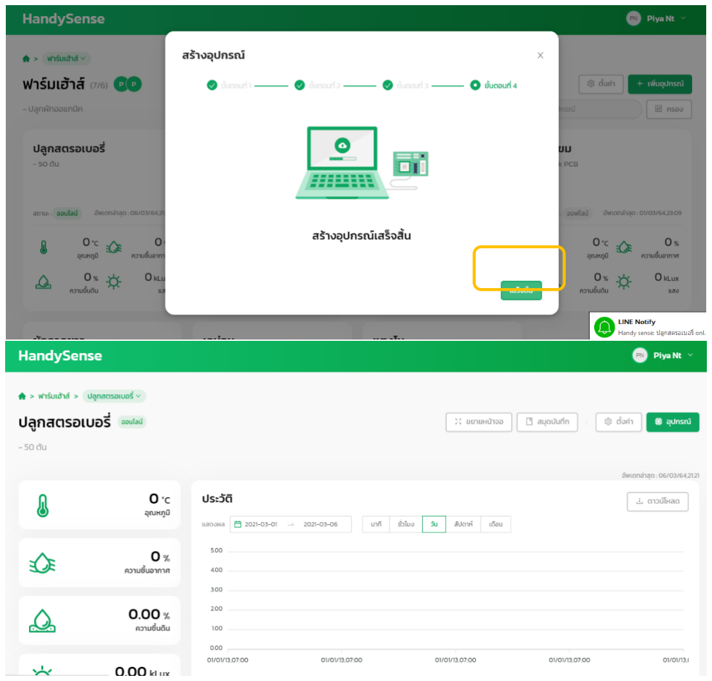
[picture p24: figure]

- ขั้นตอนที่ 12 ให้กด “เสร็จสิ้น” เพียงเท่านี้ก็สามารใช้บอร์ด HandySense ผ่านเว็บ HandySense ได้ แล้ว

คู่มือการใช้งานบอร์ด HandySense | 25

ข้อมูลติดต่อ:
ศูนย์เทคโนโลยีอิเล็กทรอนิกส์และคอมพิวเตอร์แห่งชาติ (ศอ.)
เบอร์โทรศัพท์: 025646900ต่อ2353,2366
Facebook:

HandySense Community

ทีมผู้พัฒนา:

นาย นริชพันธ์ เป็นผลดี (นักวิจัย)
- ระบบการจัดการฟาร์มที่แม่นย า
- IOT เทคโนโลยีเซนเซอร์ส าหรับการวัดและควบคุมปัจจัยเพื่อการเกษตร
- เทคโนโลยีเซนเซอร์การเกษตร

นาย พุฒิพงศ์ สุขรัตน์ (ผู้ช่วยนักวิจัย)

- วิศวกรรมซอฟต์แวร์(Software Engineer)

นาย ปิยะ ชาติไทยเจริญ (ผู้ช่วยนักวิจัย)

- ระบบฝังตัว (Embedded System)

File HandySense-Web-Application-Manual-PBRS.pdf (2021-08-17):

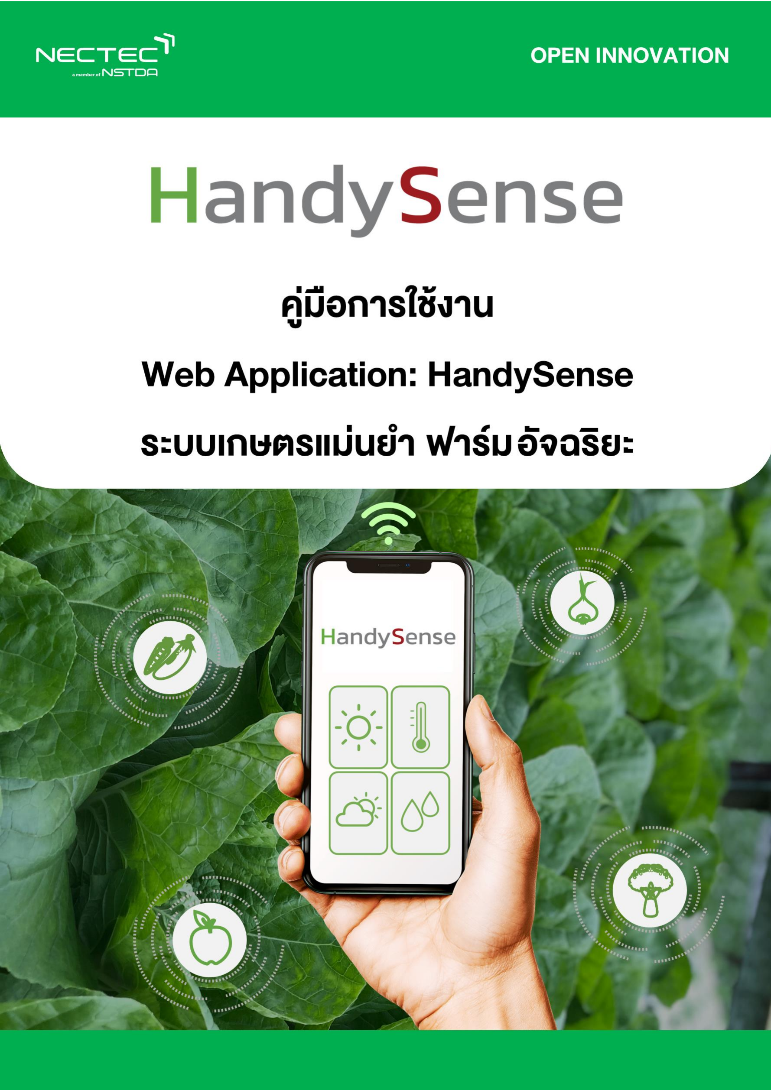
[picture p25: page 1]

คู่มือการใช้งานเว็บแอปพลิเคชัน HandySense | (ก)

สารบัญ

คู่มือการใช้งานเว็บแอปพลิเคชัน HandySense | (ข)

สารบัญรูปภาพ

คู่มือการใช้งานเว็บแอปพลิเคชัน HandySense | (ข)

คู่มือการใช้งานเว็บแอปพลิเคชัน HandySense | 1

### 1. HandySense คืออะไร

รูปที่ 1 แสดงหน้าเว็บไซต์ HandySense

HandySense คือ เว็บไซต์ระบบเกษตรอัจฉริยะที่แสดงค่าข้อมูลปัจจัยในการควบคุมผลผลิตทางการเกษตร โดยใช้เทคโนโลยีเซนเซอร์เข้ามาช ่วยในกระบวนการเพาะปลูกซึ ่งช่วยให้เกษตรกรสามารถควบคุมสภาวะ แวดล้อมในการปลูกได้ตั้งแต่เริ่มต้นส่งผลให้สามารถควบคุมคุณภาพและประเมินปริมาณผลผลิตรวมถึงช ่วย เรื่องการเพิ่มคุณค่าของผลผลิตได้โดยใช้การควบคุมกระบวนการเพาะปลูกเพื่อให้ผลผลิตออกในช่วงที่มีความ ต้องการหรือผลผลิตขาดแคลนรวมถึงการช่วยเกษตรกรน าองค์ความรู้ที่เกิดจากทักษะที่ไม่สามารถถ่ายทอดให้ เข้าใจได้เนื่องจากเป็นภูมิปัญญาและเป็นการท าเกษตรกรรมแบบวิถีชาวบ้านโดยการลองผิดลองถูกหรือเป็น องค์ความรู้ที่สืบทอดต่อกัน

คู่มือการใช้งานเว็บแอปพลิเคชัน HandySense | 2

### 2. ลงทะเบียน/เข้าสู่ระบบ

กรณีเข้าใช้งานครั้งแรก ระบบจะให้ท าการลงทะเบียนหน้า Login ผ่าน https://dashboard.handysense.io ก่อน จากนั้นสามารถเข้าสู่ระบบได้จาก Account ที่สมัครไว้ถ้าหากยังไม่เคยลงททะเบียนใหเคลิกลงทะเบียน ก่อน

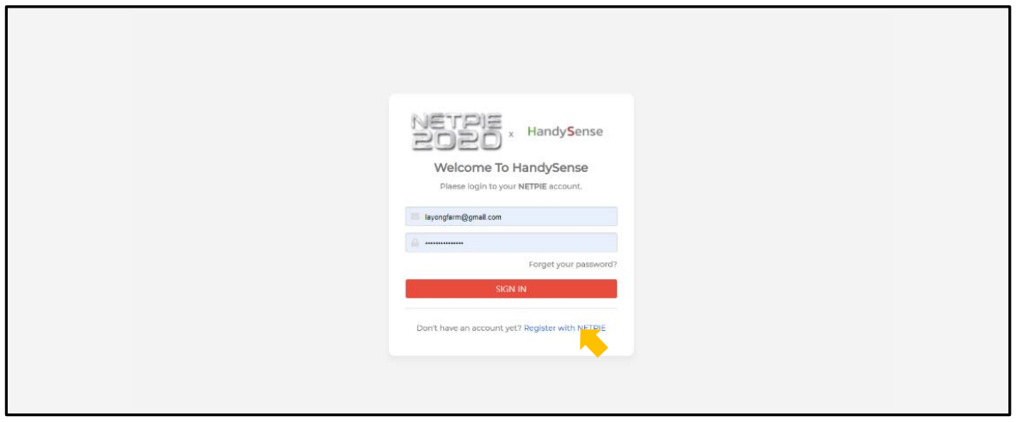
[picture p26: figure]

รูปที่ 2 แสดงการเข้าสู่ระบบจากเว็บ NETPIE

### 2.1 กรณีลืมรหัสผ่าน

กรณีลืมรหัสผ่าน (Forgot Password) ให้ผู้ใช้งานท าตามขั้นตอนต่อไปนี้

1. เมื่อเข้าสู่หน้า Login ให้คลิก Forgot Your Password?

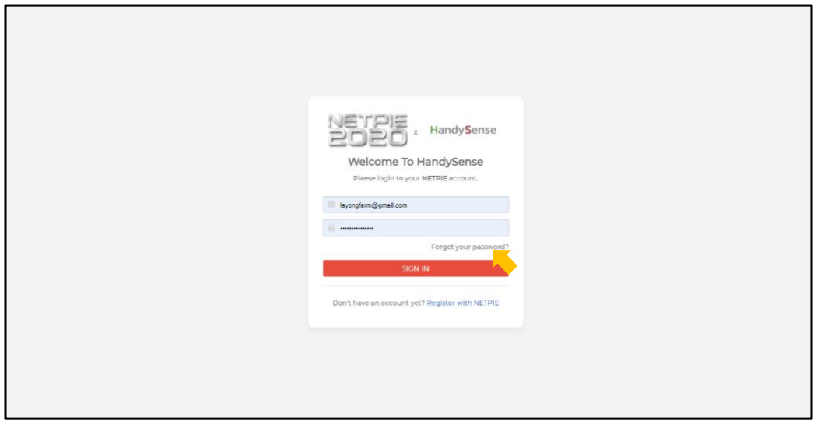
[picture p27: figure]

คู่มือการใช้งานเว็บแอปพลิเคชัน HandySense | 3
2. เมื่อเข้าสู่หน้า Forgot Password ให้กรอก Email Address ที่ผู้ใช้งานลงทะเบียนไว้
3. คลิก Reset Password จะได้รับข้อความแจ้งให้ผู้ใช้งานรับ Password ใหม่ ใน Email ที่ผู้ใช้งาน ลงทะเบียนไว้
4. เข้า Email ที่ท าการลงทะเบียนไว้ แล้วน ารหัสที่ได้กรอกที่ช่อง Password

คู่มือการใช้งานเว็บแอปพลิเคชัน HandySense | 4
5. จากนั้นคลิก Sign In ผู้ใช้งานสามารถ Login โดยใช้รหัสผ่านใหม่ได้ทันที

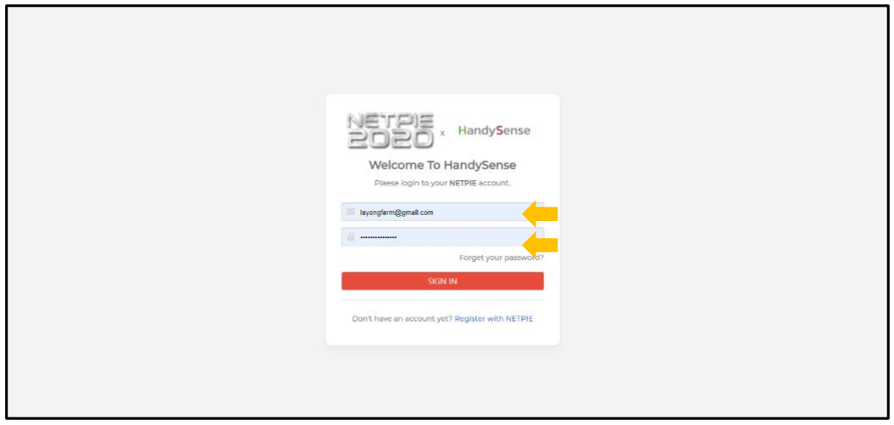
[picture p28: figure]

รูปที่ 3 แสดงการเข้าสู่ระบบส าหรับผู้ที่มีแอคเคาท์ กรณีลืมรหัสผ่าน

### 3. หน้าหลัก 3.1 หน้าแรก

เป็นหน้าที่ผู้ใช้งานจะพบหลังจาก Login ส าเร็จ ภายในหน้านี้จะแสดงรายการการ์ดของแต่ละฟาร์ม

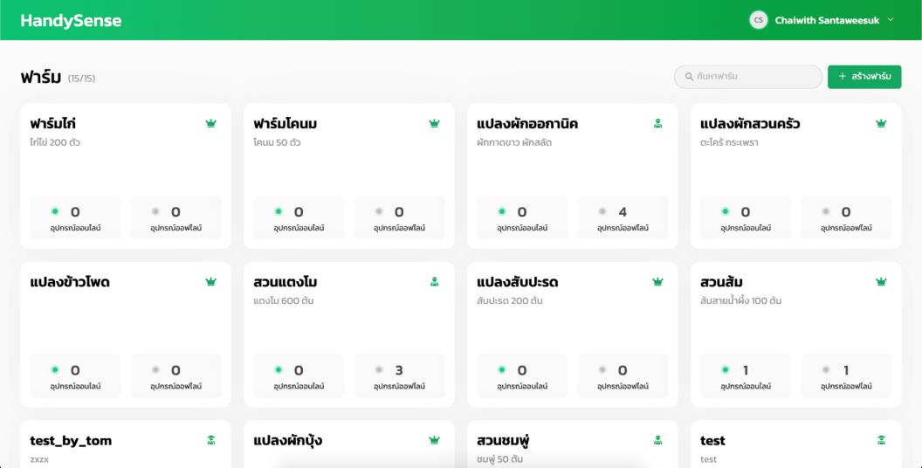
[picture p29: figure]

รูปที่ 4 แสดงหน้าหลักของเว็บไซต์ HandySense

คู่มือการใช้งานเว็บแอปพลิเคชัน HandySense | 5

### 3.2 องค์ประกอบของการ์ด

รูปที่ 5 แสดงองค์ประกอบของการ์ดฟาร์ม

### 3.3 การสร้างฟาร์ม

การสร้างฟาร์มใหม่หน้านี้สามารถท าได้โดย
1. คลิกปุ่ม “สร้างฟาร์ม”
2. กรอกชื่อฟาร์ม และรายละเอียดของฟาร์ม
3. คลิกปุ่ม “สร้าง”

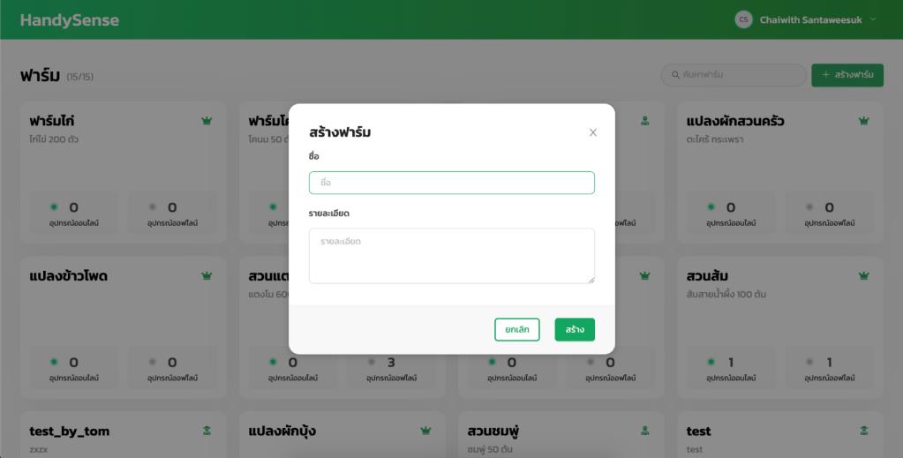
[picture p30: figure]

คู่มือการใช้งานเว็บแอปพลิเคชัน HandySense | 6

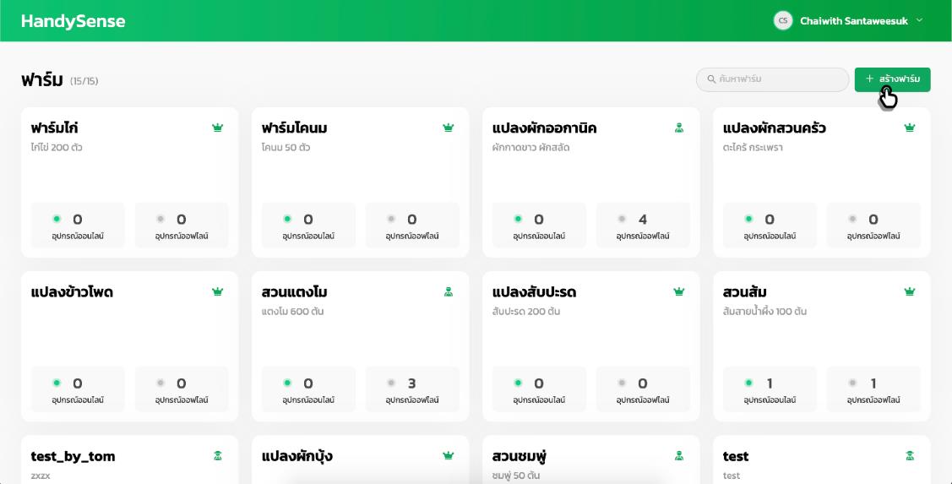
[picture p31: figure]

รูปที่ 6 แสดงการสร้างฟาร์ม

### 3.4 การจัดการข้อมูลส่วนตัว

การจัดการข้อมูลส่วนตัวปรากฏอยู่มุมขวาด้านบนของเว็บไซต์ ประกอบด้วย 3 ส่วน ได้แก่

- ข้อมูลส่วนตัว
- บัญชีการใช้งาน
- ลงชื่อออกจากระบบ

### 3.4.1 ข้อมูลส่วนตัว

เป็นส ่วนแสดงข้อมูลส ่วนตัวของผู้ใช้งาน โดยสามารถแก้ไขชื ่อและนามสกุล รวมถึงเปลี ่ยน รหัสผ่านได้

คู่มือการใช้งานเว็บแอปพลิเคชัน HandySense | 7

รูปที่ 7 แสดงข้อมูลส่วนตัว

### 3.4.2 บัญชีการใช้งาน

เป็นส่วนแสดงจ านวนข้อมูลที่มีการใช้งาน โดยแบ่งสี เป็น 2 สี ได้แก่

- สีเขียว คือ โปรเจกต์ HandySense
- สีแดง คือ โปรเจกต์อื่น ๆ

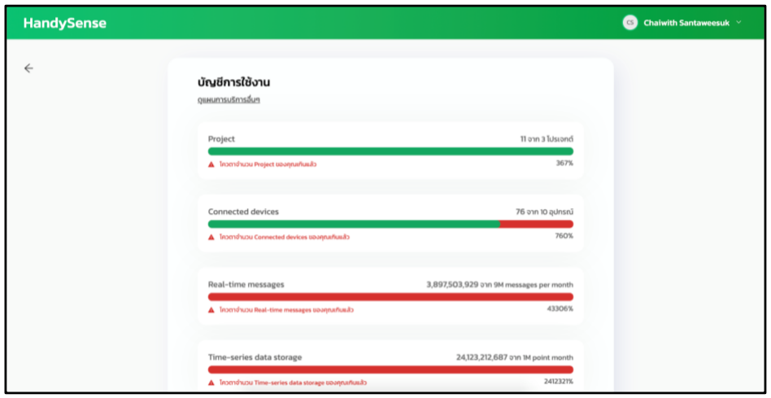
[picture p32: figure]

รูปที่ 8 แสดงบัญชีการใช้งาน

คู่มือการใช้งานเว็บแอปพลิเคชัน HandySense | 8

### 3.4.2 การลงชื่อออกจากระบบ

เมื่อผู้ใช้งานต้องการออกจากระบบ ให้ท าตามขั้นตอนต่อไปนี้

รูปที่ 9 แสดงการลงชื่อออกจากระบบ

### 4. หน้าฟาร์ม

ภายในหน้านี้จะแสดงข้อมูลต่าง ๆ ของฟาร์ม ได้แก่

- ชื่อฟาร์มและรายละเอียดของฟาร์ม
- การ์ด overview ของอุปกรณ์
- จ านวนอุปกรณ์ภายในฟาร์ม
- ชื่อสมาชิกในฟาร์ม
- ปุ่มเพิ่มอุปกรณ์
- ตั้งค่าฟาร์ม
- การกรองและการค้นหาอุปกรณ์

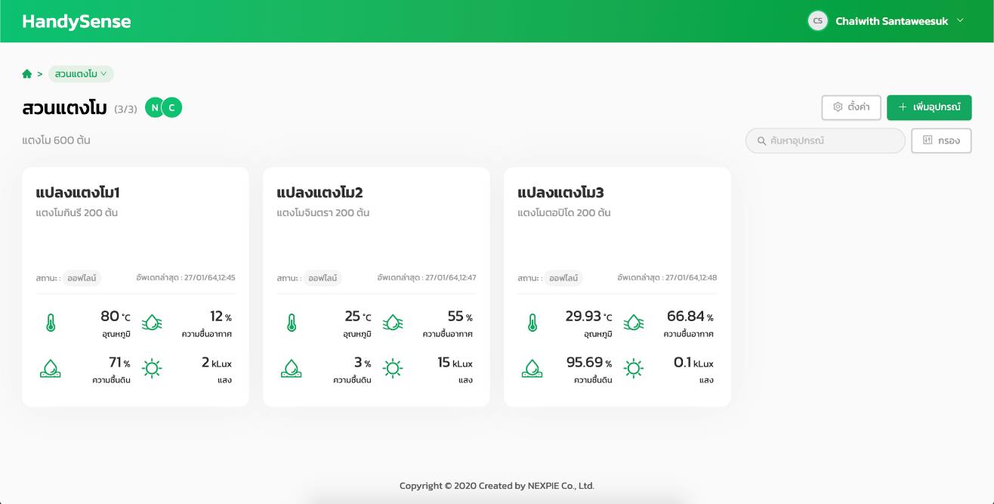
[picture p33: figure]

รูปที่ 10 แสดงหน้าฟาร์ม

คู่มือการใช้งานเว็บแอปพลิเคชัน HandySense | 9

### 4.1 องค์ประกอบของการ์ด

รูปที่ 11 แสดงองค์ประกอบของการ์ดอุปกรณ์

### 4.2 การเพิ่มอุปกรณ์

มีขั้นตอนการเพิ่ม ดังนี้
1. คลิกปุ่ม “เพิ่มอุปกรณ์”

รูปที่ 12 แสดงขั้นตอนการเพิ่มอุปกรณ์
2. คลิกปุ่ม “สร้างอุปกรณ์”

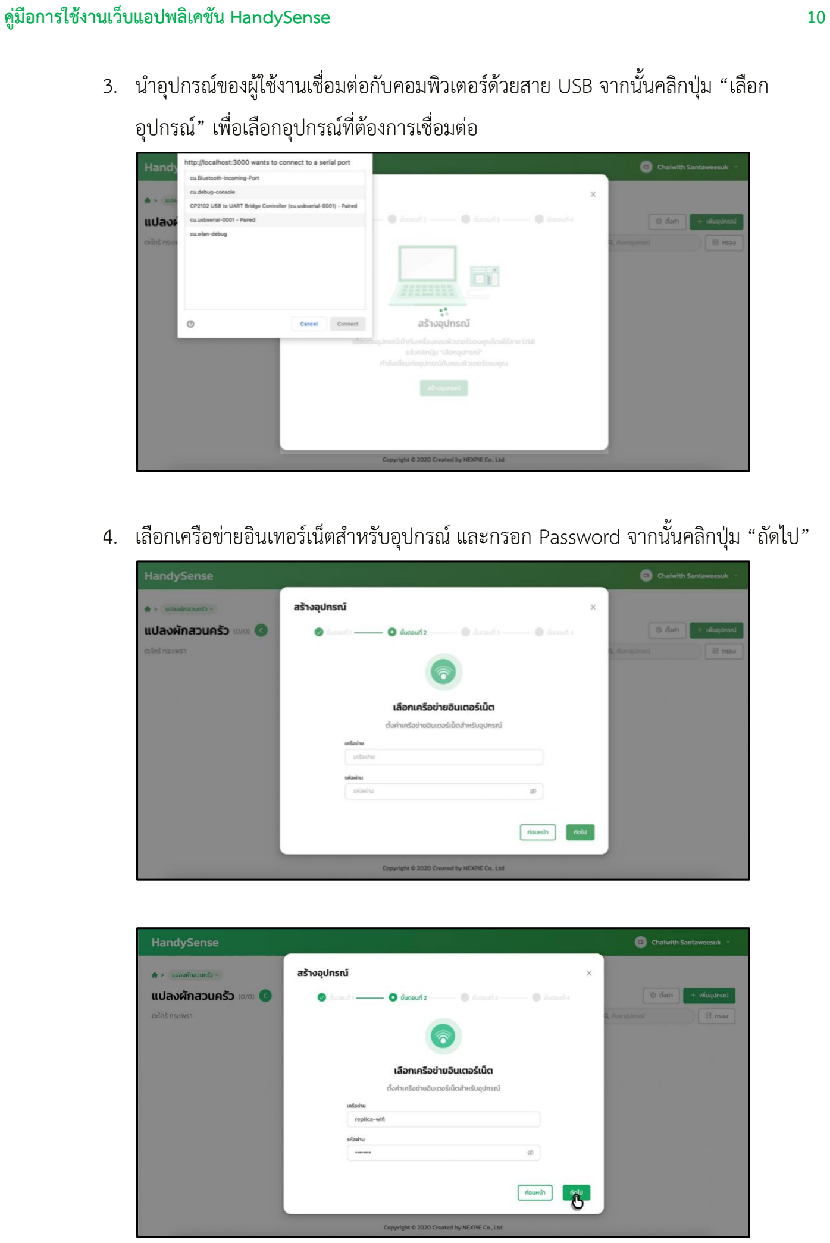
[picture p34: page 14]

คู่มือการใช้งานเว็บแอปพลิเคชัน HandySense | 10
3. น าอุปกรณ์ของผู้ใช้งานเชื่อมต่อกับคอมพิวเตอร์ด้วยสาย USB จากนั้นคลิกปุ่ม “เลือก อุปกรณ์” เพื่อเลือกอุปกรณ์ที่ต้องการเชื่อมต่อ
4. เลือกเครือข่ายอินเทอร์เน็ตส าหรับอุปกรณ์ และกรอก Password จากนั้นคลิกปุ่ม “ถัดไป”

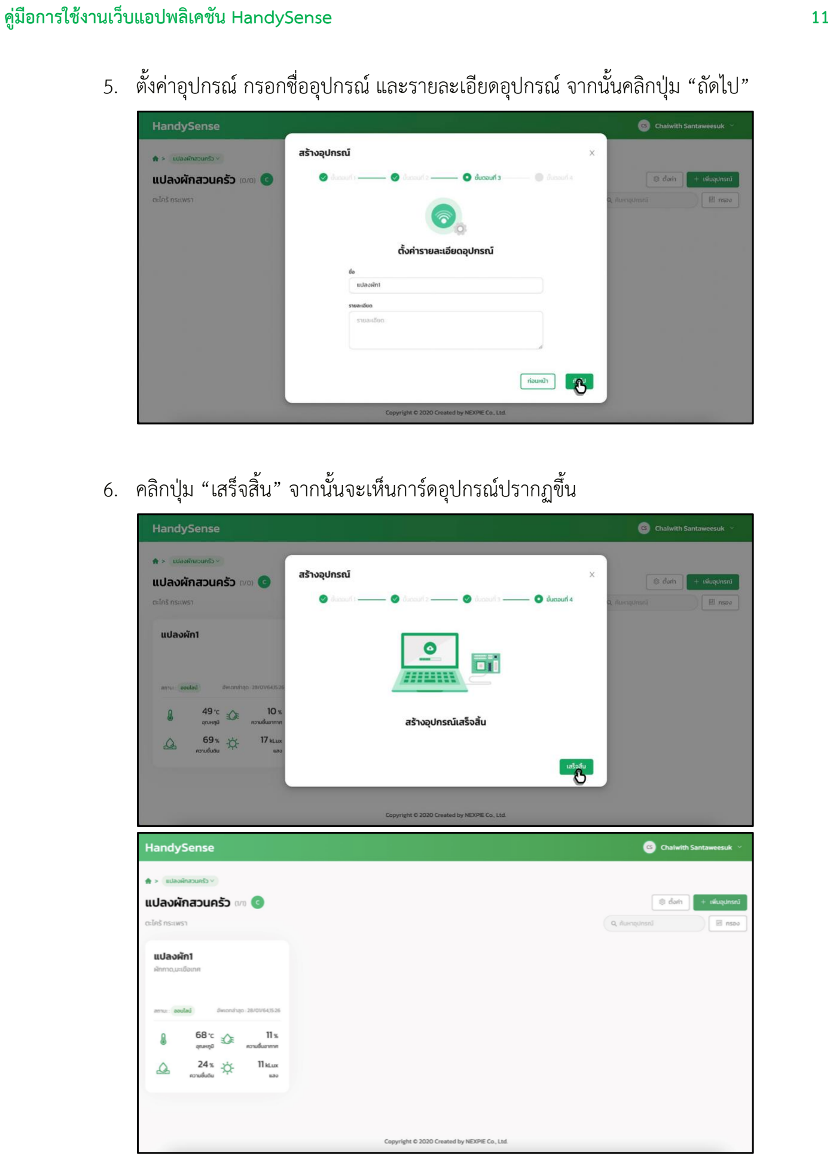
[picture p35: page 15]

คู่มือการใช้งานเว็บแอปพลิเคชัน HandySense | 11
5. ตั้งค่าอุปกรณ์ กรอกชื่ออุปกรณ์ และรายละเอียดอุปกรณ์ จากนั้นคลิกปุ่ม “ถัดไป”
6. คลิกปุ่ม “เสร็จสิ้น” จากนั้นจะเห็นการ์ดอุปกรณ์ปรากฏขึ้น

คู่มือการใช้งานเว็บแอปพลิเคชัน HandySense | 12

### 4.3 การแก้ไขอุปกรณ์

เมื่อต้องการแก้ไขข้อมูลของอุปกรณ์ จะมีขั้นตอนดังนี้

1. คลิกปุ่ม “เชื่อมต่ออุปกรณ์”

รูปที่ 13 แสดงขั้นตอนการแก้ไขอุปกรณ์

2. น าอุปกรณ์ของผู้ใช้งาน เชื่อมต่อกับคอมพิวเตอร์ด้วยสาย USB จากนั้น คลิกปุ่ม “เลือกอุปกรณ์” เพื่อเลือกอุปกรณ์ที่ต้องการเชื่อมต่อ

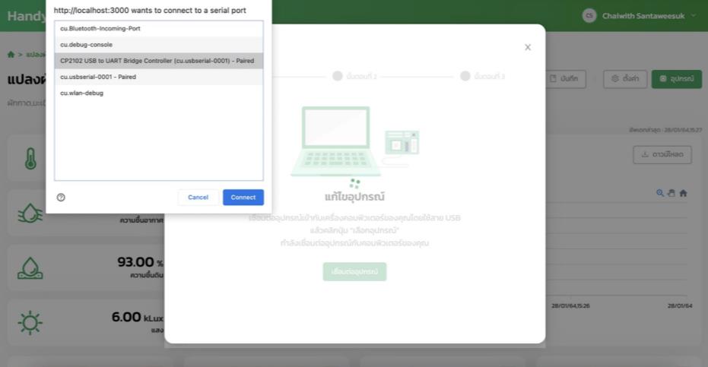
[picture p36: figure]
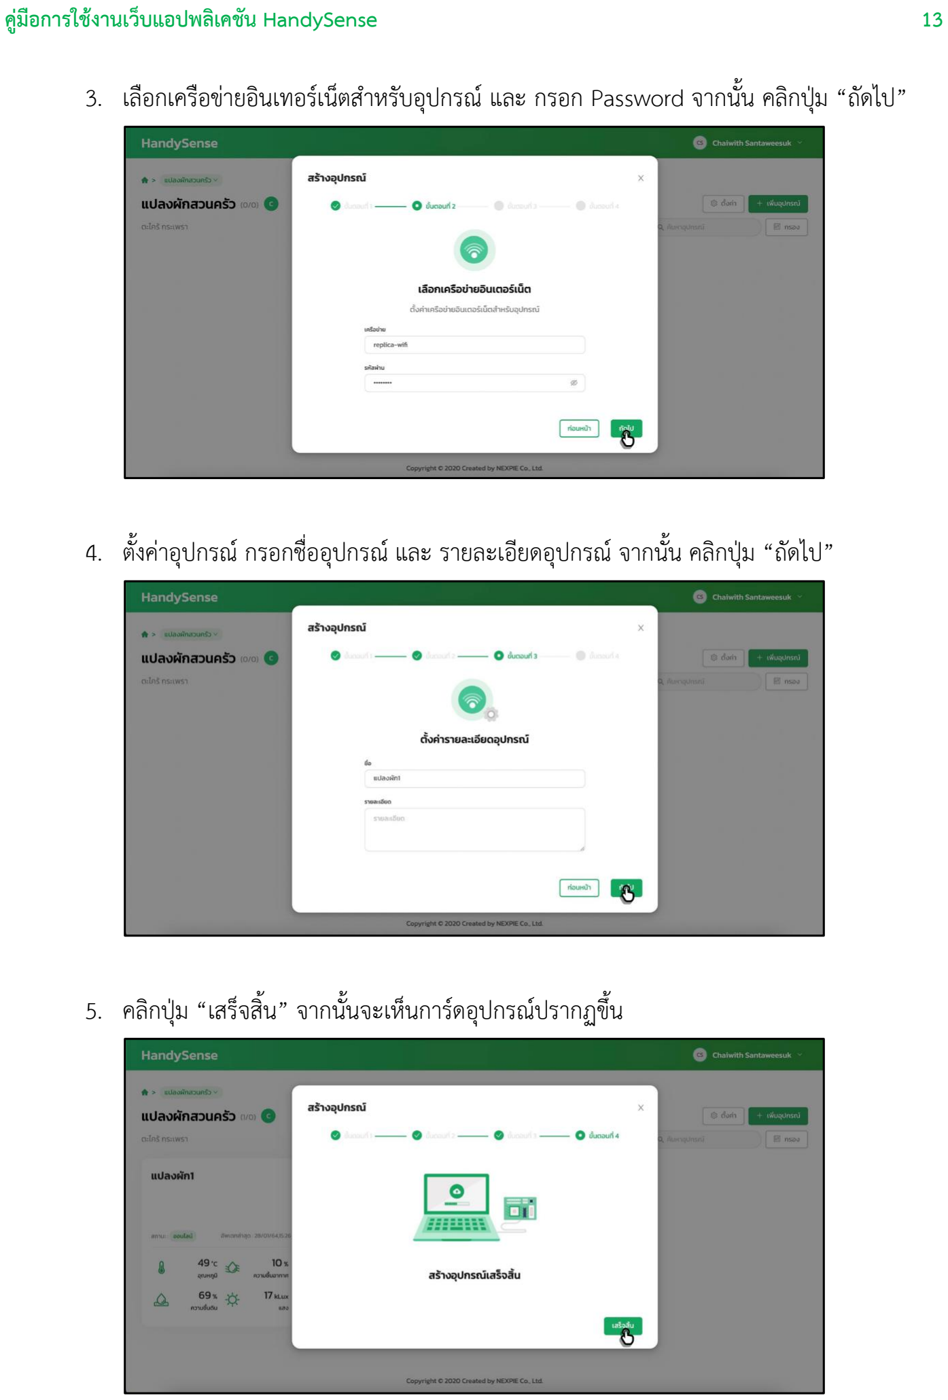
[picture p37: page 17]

คู่มือการใช้งานเว็บแอปพลิเคชัน HandySense | 13
3. เลือกเครือข่ายอินเทอร์เน็ตส าหรับอุปกรณ์ และ กรอก Password จากนั้น คลิกปุ่ม “ถัดไป”
4. ตั้งค่าอุปกรณ์ กรอกชื่ออุปกรณ์ และ รายละเอียดอุปกรณ์ จากนั้น คลิกปุ่ม “ถัดไป”
5. คลิกปุ่ม “เสร็จสิ้น” จากนั้นจะเห็นการ์ดอุปกรณ์ปรากฏขึ้น

คู่มือการใช้งานเว็บแอปพลิเคชัน HandySense | 14

### 4.4 การตั้งค่า

การตั้งค่าจะแบ่งเป็น 2 ส่วน ได้แก่ 1) การตั้งค่าฟาร์ม 2) การตั้งค่าสมาชิก

รูปที่ 14 แสดงการตั้งค่าฟาร์ม

### 4.4.1 การตั้งค่าฟาร์ม

คือ ส่วนตั้งค่าข้อมูลต่าง ๆ ของฟาร์ม จะแบ่งการตั้งค่าเป็น 2 ส่วน ได้แก่

### 1. การตั้งค่าทั่วไป คือ ส่วนตั้งค่าชื่อฟาร์ม และรายละเอียดของฟาร์ม

รูปที่ 15 แสดงการตั้งค่าทั่วไปของฟาร์ม

### 2. ตั้งค่าการแจ้งเตือน คือ ส่วนตั้งค่าการแจ้งเตือนฟาร์ม สามารถกรอก Line Token และ

สามารถเปิด/ปิดการแจ้งเตือนของฟาร์มผ่าน Line Notify ได้

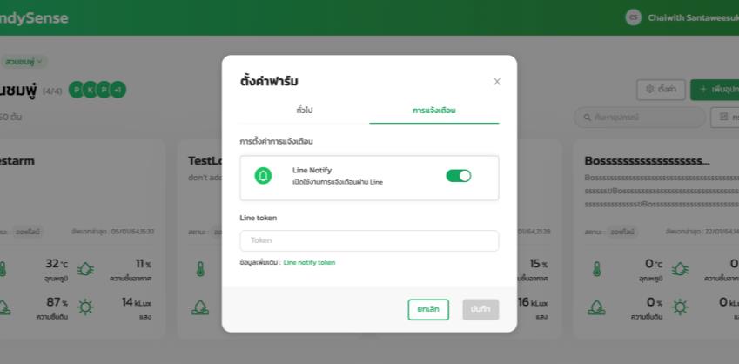
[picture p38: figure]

รูปที่ 16 แสดงการตั้งค่าการแจ้งเตือนฟาร์ม

คู่มือการใช้งานเว็บแอปพลิเคชัน HandySense | 15

### 4.4.2 การตั้งค่าสมาชิก

คือ ส่วนตั้งค่าสมาชิก สามารถเพิ่ม-ลบสมาชิก และกรอกสถานะสิทธิ์ของผู้ใช้งาน

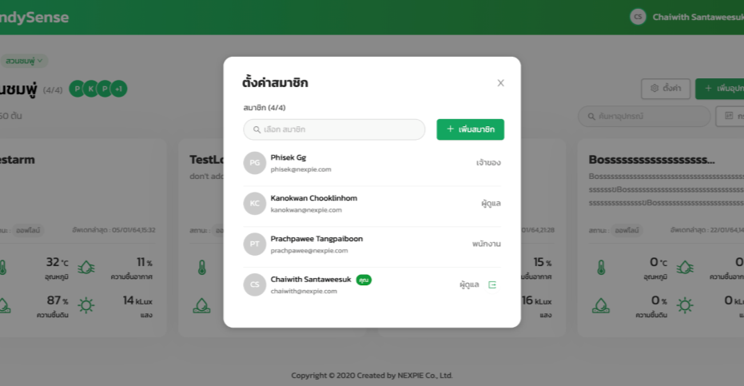
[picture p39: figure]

รูปที่ 17 แสดงการตั้งค่าสมาชิก

- สถานะสิทธิ์ของผู้ใช้งาน มี 3 แบบ ได้แก่

### 1. สิทธิ์เจ้าของ สามารถมองเห็น สร้างและแก้ไขข้อมูลทุกอย่างภายในโปรเจกต์

รูปที่ 18 แสดงรูปสิทธิ์เจ้าของ

### 2. สิทธิ์ผู้ดูแล สามารถมองเห็นโปรเจกต์ สร้าง แก้ไข และลบอุปกรณ์ของฟาร์ม รวมถึง

สามารถแก้ไขการตั้งค่าอุปกรณ์ของฟาร์ม

คู่มือการใช้งานเว็บแอปพลิเคชัน HandySense | 16

รูปที่ 19 แสดงรูปสิทธิ์ผู้ดูแล

### 3. สิทธิ์พนักงาน สามารถมองเห็นโปรเจกต์และแก้ไขการตั้งค่าอุปกรณ์ของฟาร์มได้

รูปที่ 20 แสดงรูปสิทธิ์พนักงาน

### 5. หน้าอุปกรณ์

ภายในหน้าหน้าอุปกรณ์จะแสดงข้อมูลต่าง ๆ ของอุปกรณ์ ได้แก่

- ชื่ออุปกรณ์และรายละเอียดของอุปกรณ์
- สถานะของอุปกรณ์
- ค่าเซนเซอร์ของอุปกรณ์
- ประวัติค่าเซนเซอร์ของอุปกรณ์
- เวลาอัปเดตข้อมูลล่าสุด
- ตั้งค่าการท างานสวิตช์
- ปุ่มแก้ไขอุปกรณ์
- ตั้งค่าฟาร์ม
- บันทึกโน้ต
- การขยาย / ย่อหน้าจอ

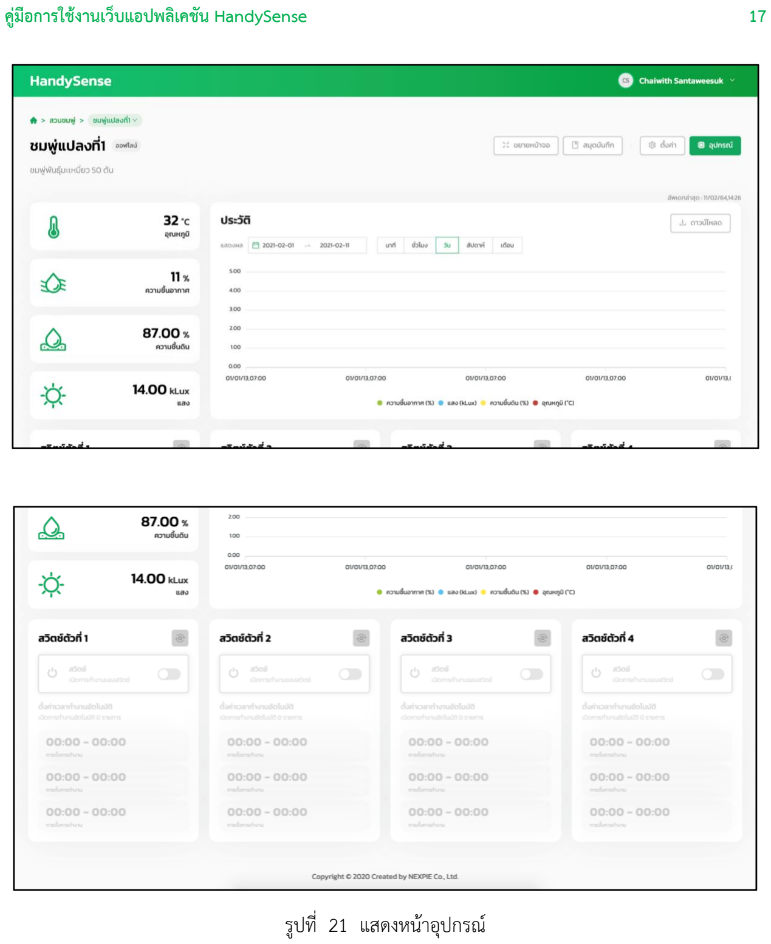
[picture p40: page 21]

คู่มือการใช้งานเว็บแอปพลิเคชัน HandySense | 17

รูปที่ 21 แสดงหน้าอุปกรณ์

คู่มือการใช้งานเว็บแอปพลิเคชัน HandySense | 18

### 5.1 ค่าเซนเซอร์ของอุปกรณ์

คือ ส่วนที่แสดงเซนเซอร์ต่าง ๆ ของอุปกรณ์ ได้แก่ ค่าอุณหภูมิ ค่าความชื้นอากาศ ค่าความชื้นดิน ค ่าปริมาณแสง ค ่าเซนเซอร์เหล ่านี้จะช ่วยให้เกษตรกรควบคุมการเจริญเติบโตของพืชให้อยู ่ในสภาวะที่ เหมาะสมตลอดช่วงอายุ


รูปที่ 22 แสดงค่าเซนเซอร์ของอุปกรณ์

### 5.2 ตั้งค่าการท างานสวิตช์

คือ ส่วนแสดงการตั้งค่าสวิตช์ต่าง ๆ ได้แก่

รูปที่ 23 แสดงการตั้งค่าการท างานสวิตซ์

คู่มือการใช้งานเว็บแอปพลิเคชัน HandySense | 19

### 5.2.1 การเปิด/ปิดการท างานของสวิตช์ เมื่อต้องการเปิดหรือปิดสวิตช์ของอุปกรณ์ สามารถ

เลือกที่ส่วนนี้เพื่อเปิดปิดการท างานของสวิตช์ได้

รูปที่ 24 แสดงการเปิด/ปิดการท างานสวิตซ์

### 5.2.2 การตั้งเวลาการท างานอัตโนมัติของสวิตช์เมื่อต้องการตั้งเวลาการท างานอัตโนมัติของ

สวิตช์ สามารถเลือกที่ส่วนนี้เพื่อตั้งช่วงเวลาให้สวิตช์ท างานตามเวลาที่ก าหนดไว้


รูปที่ 25 แสดงการตั้งเวลาการท างานสวิตช์

คู่มือการใช้งานเว็บแอปพลิเคชัน HandySense | 20

### 5.2.3 การตั้งค่าการท างานอัตโนมัติเมื่อต้องการตั้งเวลาการท างานสวิตช์ของอุปกรณ์แบบ

อัตโนมัติ สามารถเลือกที ่ส ่วนนี้ สวิตช์จะท างานเปิด-ปิดอัตโนมัติตามค ่าต ่าสุดและ ค่าสูงสุด ตามที่ก าหนดค่าไว้

รูปที่ 26 แสดงการตั้งค่าการท างานอัตโนมัติ

### 5.3 การแก้ไขอุปกรณ์

เมื่อต้องการแก้ไขข้อมูลของอุปกรณ์ จะมีขั้นตอนดังนี้

1. คลิกปุ่ม “เชื่อมต่ออุปกรณ์”


รูปที่ 27 แสดงขั้นตอนการแก้ไขอุปกรณ์


คู่มือการใช้งานเว็บแอปพลิเคชัน HandySense | 21
2. น าอุปกรณ์ของผู้ใช้งาน เชื่อมต่อกับคอมพิวเตอร์ด้วยสาย USB จากนั้น คลิกปุ่ม “เลือกอุปกรณ์” เพื่อเลือกอุปกรณ์ที่ต้องการเชื่อมต่อ
3. เลือกเครือข่ายอินเทอร์เน็ตส าหรับอุปกรณ์ และ กรอก Password จากนั้น คลิกปุ่ม “ถัดไป”
4. ตั้งค่าอุปกรณ์ กรอกชื่ออุปกรณ์ และ รายละเอียดอุปกรณ์ จากนั้น คลิกปุ่ม “ถัดไป”

คู่มือการใช้งานเว็บแอปพลิเคชัน HandySense | 22
5. คลิกปุ่ม “เสร็จสิ้น” จากนั้นจะเห็นการ์ดอุปกรณ์ปรากฏขึ้น

### 5.4 การตั้งค่าอุปกรณ์

คือ ส่วนตั้งค่าข้อมูลต่าง ๆ ของอุปกรณ์ จะแบ่งการตั้งค่าเป็น 2 ส่วน ได้แก่

### 5.4.1 ตั้งค่าทั่วไป คือ ส่วนตั้งค่าชื่ออุปกรณ์และรายละเอียดของอุปกรณ์


รูปที่ 28 แสดงการตั้งค่าทั่วไปของอุปกรณ์

### 5.4.2 ตั้งค่าการแจ้งเตือน คือ ส่วนตั้งค่าการแจ้งเตือนอุปกรณ์ สามารถเปิด-ปิดการแจ้ง

เตือนสถานะของอุปกรณ์ รวมถึงสามารถเปิด-ปิดการแจ้งเตือน การท างานของสวิตช์แต่ละตัวได้


รูปที่ 29 แสดงการตั้งค่าการแจ้งเตือนอุปกรณ์

คู่มือการใช้งานเว็บแอปพลิเคชัน HandySense | 23

### 5.5 การบันทึกข้อความ

เมื่อต้องการบันทึกข้อความสามารถกดที่ปุ่ม “สมุดบันทึก” เพื่อเข้าไปบันทึกข้อความ หรือ บันทึก ข้อมูลของอุปกรณ์

รูปที่ 30 แสดงการบันทึกข้อความ

### 5.6 การขยายและย่อหน้าจอ

เมื่อต้องการดูข้อมูลเต็มหน้าจอสามารถกดที่ปุ่ม “ขยายหน้าจอ” และเมื่อต้องการกลับสู่หน้าจอปกติ สามารถกดที่ปุ่ม “ย่อหน้าจอ”


รูปที่ 31 แสดงการตั้งค่าขยายและย่อหน้าจอ

คู่มือการใช้งานเว็บแอปพลิเคชัน HandySense | 24

ข้อมูลติดต่อ:
ศูนย์เทคโนโลยีอิเล็กทรอนิกส์และคอมพิวเตอร์แห่งชาติ (ศอ.)
เบอร์โทรศัพท์: 025646900ต่อ2353,2366
Facebook:

HandySense Community

ทีมผู้พัฒนาทางเทคโนโลยี:

นาย นริชพันธ์ เป็นผลดี (นักวิจัย)

- ระบบการจัดการฟาร์มที่แม่นย า
- IOT เทคโนโลยีเซนเซอร์ส าหรับการวัดและควบคุมปัจจัยเพื่อการเกษตร
- เทคโนโลยีเซนเซอร์การเกษตร

นาย พุฒิพงศ์ สุขรัตน์ (ผู้ช่วยนักวิจัย)

- วิศวกรรมซอฟต์แวร์(Software Engineer)

นาย ปิยะ ชาติไทยเจริญ (ผู้ช่วยนักวิจัย)

- ระบบฝังตัว (Embedded System)

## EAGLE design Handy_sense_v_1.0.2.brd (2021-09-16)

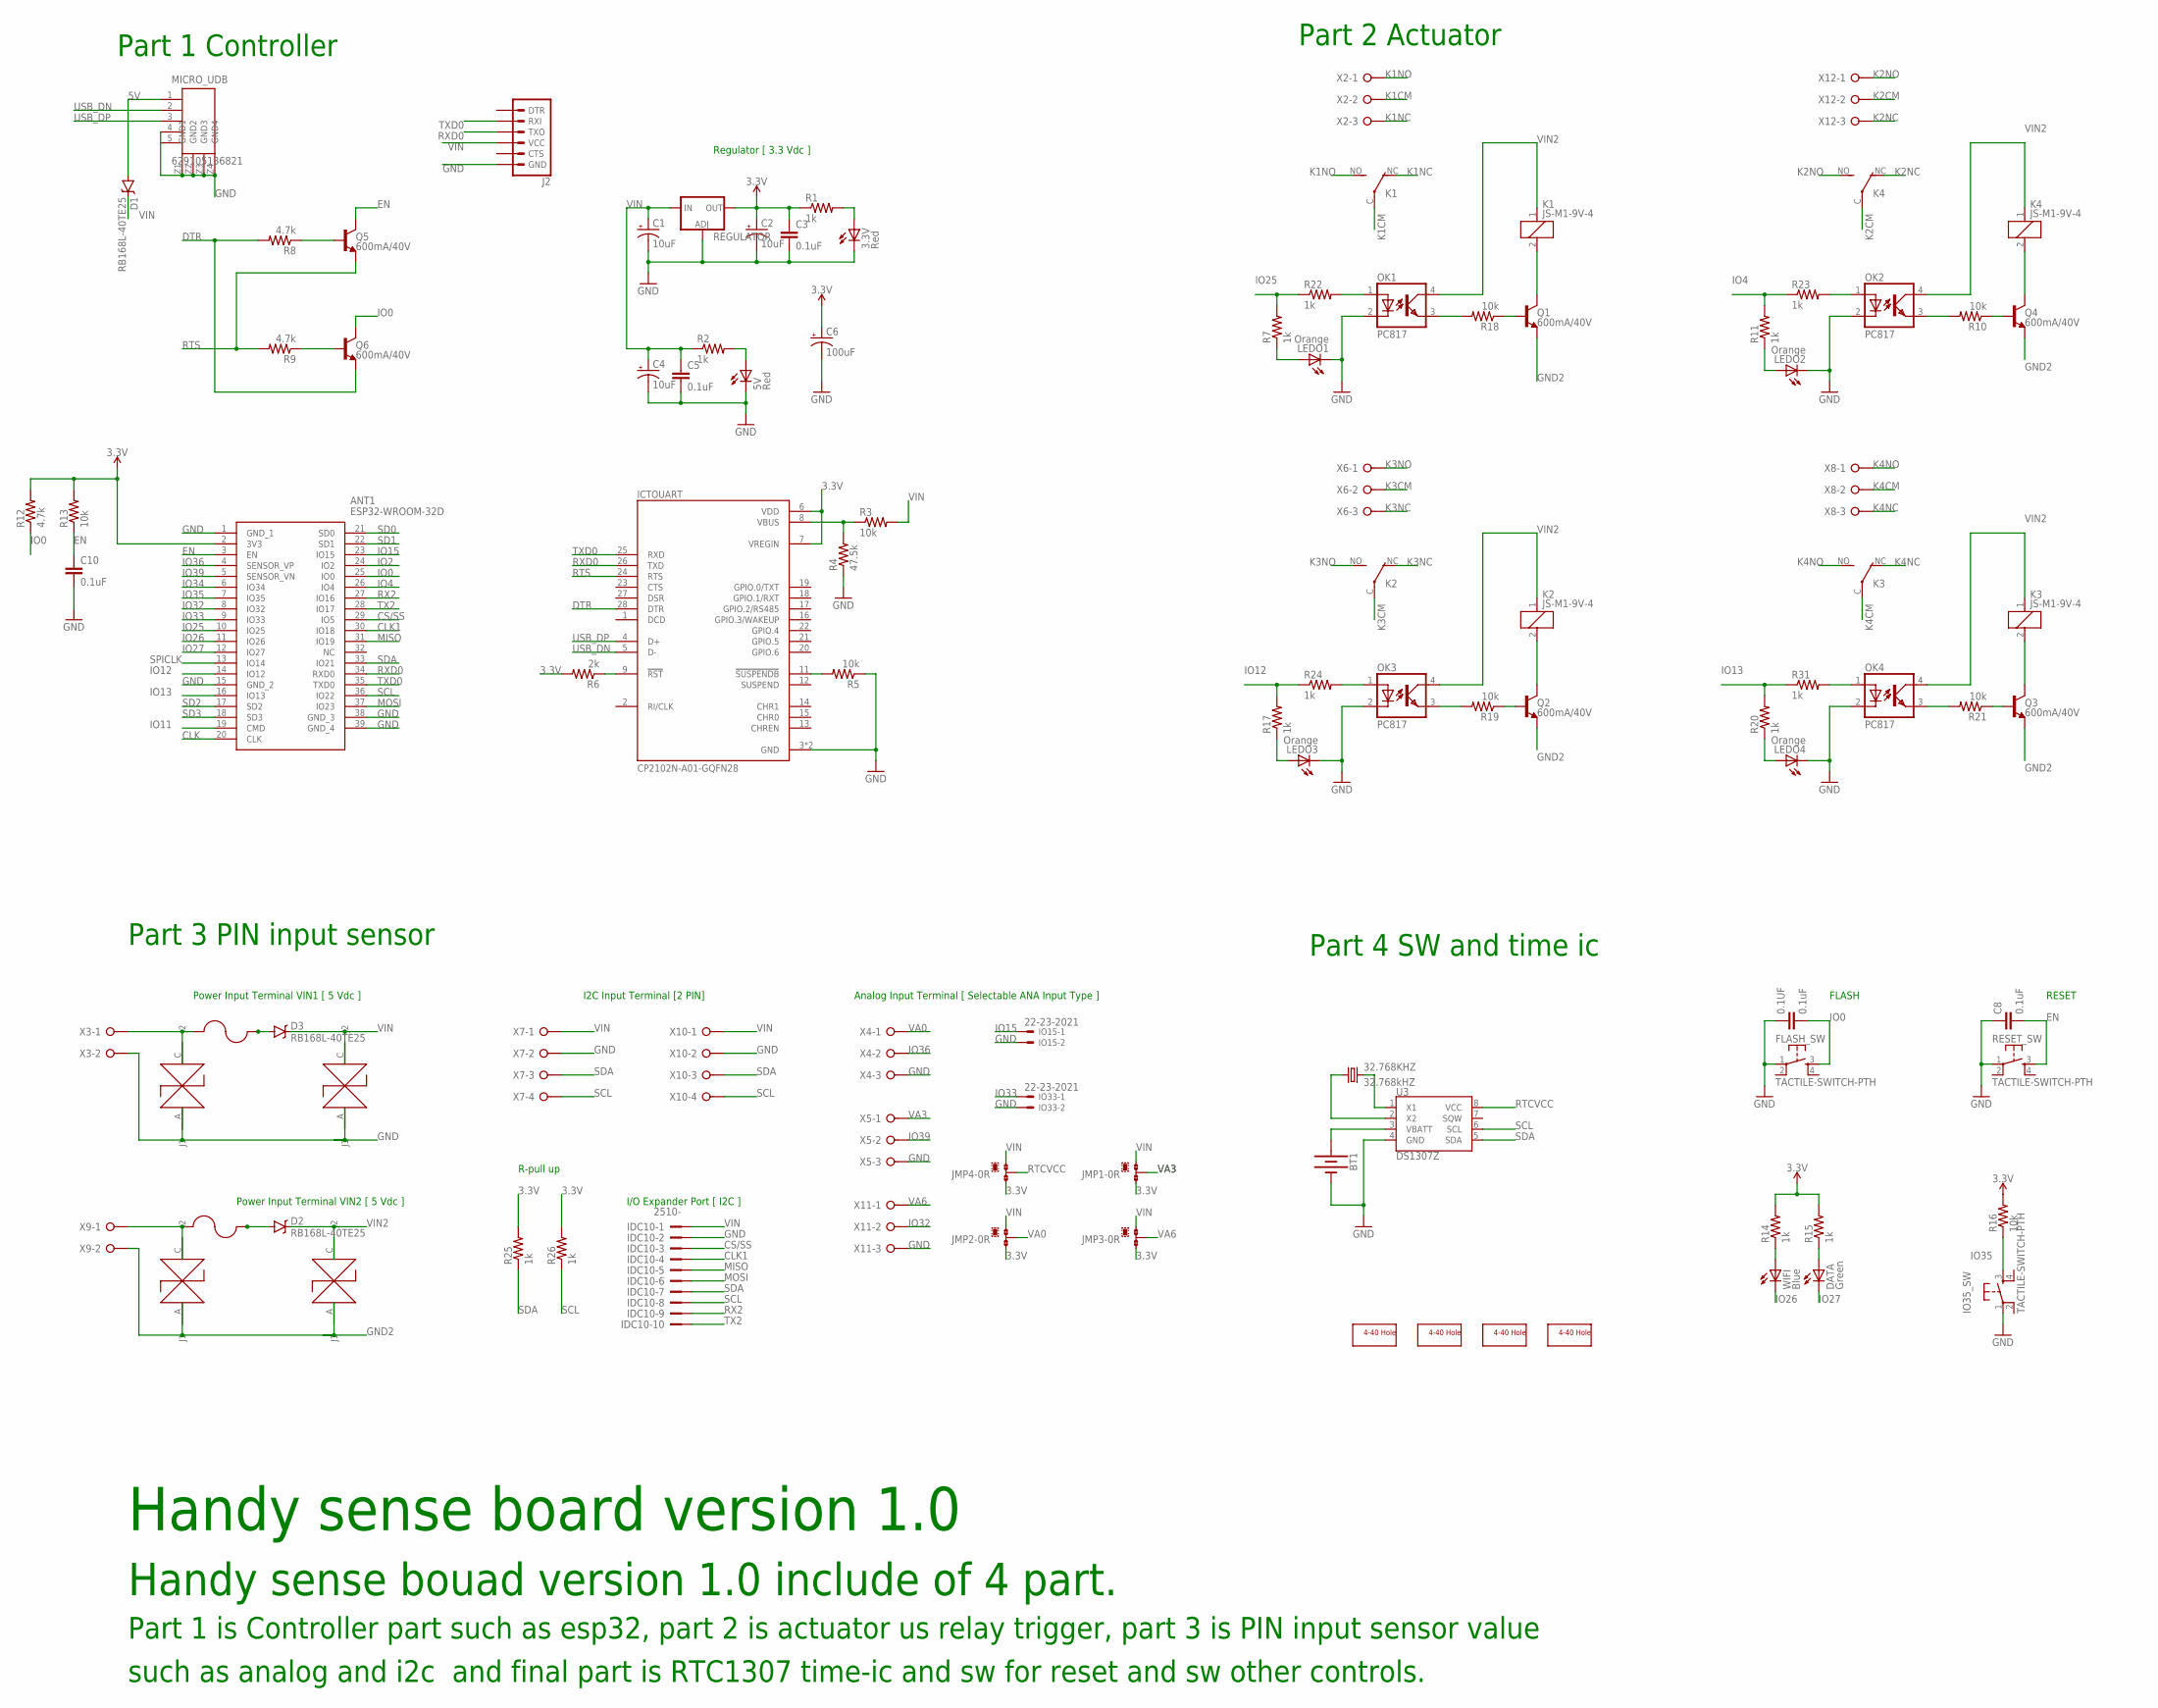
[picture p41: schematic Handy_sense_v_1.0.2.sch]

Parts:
0.1UF: 0.1uF; 0805
3.3V, 5V: Red; CHIPLED_0805
32.768KHZ: 32.768kHZ; TC26H
ANT1: ESP32-WROOM-32D; ESP32WROOM32D
BT1: BATTERY-20MM_PTH_KIT; BATTCOM_20MM_PTH_KIT
C1, C2, C4: 10uF; EIA3216
C3, C5, C8, C10: 0.1uF; 0805
C6: 100uF; EIA7343
D1, D2, D3: RB168L-40TE25; SMA-DIODE
DATA: Green; CHIPLED_0805
FLASH_SW: TACTILE-SWITCH-PTH; TAC-SWITCH-PTH
HOLE0, HOLE1, HOLE2, HOLE3: SCREW_HOLE_4-40
ICTOUART: CP2102N-A01-GQFN28; QFN50P500X500X80-29N
IDC10: 2510-; PAK100/2500-10
IO15, IO33: 22-23-2021
IO35_SW: TACTILE-SWITCH-PTH; TAC-SWITCH-PTH
J2: 6_PIN_SERIAL_TARGET_SILK; 1X06
J28CA1, J28CA3, J28CA4, J28CA6: SMBJ28CA; DIOM505270X240
JMP1, JMP2, JMP3, JMP4: 0R-JUMPB; B0R-JMP
K1, K2, K3, K4: JS-M1-9V-4; JS-M
LEDO1, LEDO2, LEDO3, LEDO4: Orange; CHIPLED_0805
MICRO_UDB: 629105136821
OK1, OK2, OK3, OK4: PC817; DIL04
Q1, Q2, Q3, Q4, Q5, Q6: 600mA/40V; SOT23-3
R1, R2, R7, R11, R14, R15, R17, R20, R22, R23, R24, R25, R26, R31: 1k; R0805
R3, R5, R10, R13, R16, R18, R19, R21: 10k; R0805
R4: 47.5k; R0805
R6: 2k; R0805
R8, R9, R12: 4.7k; R0805
REGULATOR: V_REG_LM1117SOT223; SOT223
RESET_SW: TACTILE-SWITCH-PTH; TAC-SWITCH-PTH
U3: DS1307Z; SO08-0.15
U$1, U$2: MSMFF2602; FUSE_MF-MSMF260-2
WIFI: Blue; CHIPLED_0805
X2, X4, X5, X6, X8, X11, X12: W237-03P; W237-133
X3, X9: W237-02P; W237-132
X7, X10: W237-04P; W237-4P

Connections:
3.3V: ANT1.2 (3V3), C2.A (+), C3.1, C6.A (+), ICTOUART.6 (VDD), ICTOUART.7 (VREGIN), JMP1.3, JMP2.3, JMP3.3, JMP4.3, R1.1, R6.2, R12.2, R13.2, R14.2, R15.2, R16.2, R25.2, R26.2, REGULATOR.2 (OUT), REGULATOR.4 (OUT)
5V: D1.A, MICRO_UDB.1 (+5V)
CLK: ANT1.20 (CLK)
CLK1: ANT1.30 (IO18), IDC10.4
CS/SS: ANT1.29 (IO5), IDC10.3
DTR: ICTOUART.28 (DTR), Q6.2 (E), R8.2
EN: ANT1.3 (EN), C8.2, C10.1, Q5.3 (C), R13.1, RESET_SW.3
GND: 0.1UF.1, 3.3V.C, 5V.C, ANT1.1 (GND_1), ANT1.15 (GND_2), ANT1.38 (GND_3), ANT1.39 (GND_4), BT1.2 (-), C1.C (-), C2.C (-), C3.2, C4.C (-), C5.2, C6.C (-), C8.1, C10.2, FLASH_SW.1, ICTOUART.3 (GND), ICTOUART.29 (GND), IDC10.2, IO15.2, IO33.2, IO35_SW.1, J2.6 (GND), J28CA1.A (J1), J28CA3.A (J1), LEDO1.C, LEDO2.C, LEDO3.C, LEDO4.C, MICRO_UDB.4 (ID), MICRO_UDB.5 (GND), MICRO_UDB.Z1 (GND1), MICRO_UDB.Z2 (GND2), MICRO_UDB.Z3 (GND3), MICRO_UDB.Z4 (GND4), OK1.2 (C), OK2.2 (C), OK3.2 (C), OK4.2 (C), R4.1, R5.1, REGULATOR.1 (ADJ), RESET_SW.1, U3.4 (GND), X3.2, X4.3, X5.3, X7.2, X10.2, X11.3
GND2: J28CA4.A (J1), J28CA6.A (J1), Q1.2 (E), Q2.2 (E), Q3.2 (E), Q4.2 (E), X9.2
IO0: 0.1UF.2, ANT1.25 (IO0), FLASH_SW.3, Q6.3 (C), R12.1
IO2: ANT1.24 (IO2)
IO4: ANT1.26 (IO4), R11.2, R23.1
IO11: ANT1.19 (CMD)
IO12: ANT1.14 (IO12), R17.2, R24.1
IO13: ANT1.16 (IO13), R20.2, R31.1
IO15: ANT1.23 (IO15), IO15.1
IO25: ANT1.10 (IO25), R7.2, R22.1
IO26: ANT1.11 (IO26), WIFI.C
IO27: ANT1.12 (IO27), DATA.C
IO32: ANT1.8 (IO32), X11.2
IO33: ANT1.9 (IO33), IO33.1
IO34: ANT1.6 (IO34)
IO35: ANT1.7 (IO35), IO35_SW.3, R16.1
IO36: ANT1.4 (SENSOR_VP), X4.2
IO39: ANT1.5 (SENSOR_VN), X5.2
K1CM: K1.C, X2.2
K1NC: K1.NC (O), X2.3
K1NO: K1.NO (S), X2.1
K2CM: K4.C, X12.2
K2NC: K4.NC (O), X12.3
K2NO: K4.NO (S), X12.1
K3CM: K2.C, X6.2
K3NC: K2.NC (O), X6.3
K3NO: K2.NO (S), X6.1
K4CM: K3.C, X8.2
K4NC: K3.NC (O), X8.3
K4NO: K3.NO (S), X8.1
MISO: ANT1.31 (IO19), IDC10.5
MOSI: ANT1.37 (IO23), IDC10.6
unnamed: K1.2, Q1.3 (C)
unnamed: ICTOUART.9 (!RST), R6.1
unnamed: ICTOUART.8 (VBUS), R3.1, R4.2
unnamed: 5V.A, R2.2
unnamed: Q4.1 (B), R10.1
unnamed: ICTOUART.11 (!SUSPENDB), R5.2
unnamed: Q5.1 (B), R8.1
unnamed: Q1.1 (B), R18.1
unnamed: Q2.1 (B), R19.1
unnamed: Q6.1 (B), R9.1
unnamed: OK3.3 (EMIT), R19.2
unnamed: OK1.3 (EMIT), R18.2
unnamed: 32.768KHZ.2, U3.1 (X1)
unnamed: R14.1, WIFI.A
unnamed: 3.3V.A, R1.2
unnamed: K2.2, Q2.3 (C)
unnamed: 32.768KHZ.1, U3.2 (X2)
unnamed: BT1.1 (+), U3.3 (VBATT)
unnamed: DATA.A, R15.1
unnamed: LEDO2.A, R11.1
unnamed: OK2.3 (EMIT), R10.2
unnamed: LEDO3.A, R17.1
unnamed: K4.2, Q4.3 (C)
unnamed: Q3.1 (B), R21.1
unnamed: LEDO4.A, R20.1
unnamed: OK4.3 (EMIT), R21.2
unnamed: K3.2, Q3.3 (C)
unnamed: J28CA1.C (J2), U$1.1, X3.1
unnamed: OK1.1 (A), R22.2
unnamed: OK3.1 (A), R24.2
unnamed: OK2.1 (A), R23.2
unnamed: OK4.1 (A), R31.2
unnamed: LEDO1.A, R7.1
unnamed: D3.A, U$1.2
unnamed: J28CA4.C (J2), U$2.1, X9.1
unnamed: D2.A, U$2.2
RTCVCC: JMP4.2, U3.8 (VCC)
RTS: ICTOUART.24 (RTS), Q5.2 (E), R9.2
RX2: ANT1.27 (IO16), IDC10.9
RXD0: ANT1.34 (RXD0), ICTOUART.26 (TXD), J2.3 (TXO)
SCL: ANT1.36 (IO22), IDC10.8, R26.1, U3.6 (SCL), X7.4, X10.4
SD0: ANT1.21 (SD0)
SD1: ANT1.22 (SD1)
SD2: ANT1.17 (SD2)
SD3: ANT1.18 (SD3)
SDA: ANT1.33 (IO21), IDC10.7, R25.1, U3.5 (SDA), X7.3, X10.3
SPICLK: ANT1.13 (IO14)
TX2: ANT1.28 (IO17), IDC10.10
TXD0: ANT1.35 (TXD0), ICTOUART.25 (RXD), J2.2 (RXI)
USB_DN: ICTOUART.5 (D-), MICRO_UDB.2 (D-)
USB_DP: ICTOUART.4 (D+), MICRO_UDB.3 (D+)
VA0: JMP2.2, X4.1
VA3: JMP1.2, X5.1
VA6: JMP3.2, X11.1
VIN: C1.A (+), C4.A (+), C5.1, D1.C, D3.C, IDC10.1, J2.4 (VCC), J28CA3.C (J2), JMP1.1, JMP2.1, JMP3.1, JMP4.1, R2.1, R3.2, REGULATOR.3 (IN), X7.1, X10.1
VIN2: D2.C, J28CA6.C (J2), K1.1, K2.1, K3.1, K4.1, OK1.4 (COL), OK2.4 (COL), OK3.4 (COL), OK4.4 (COL)

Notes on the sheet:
Power Input Terminal VIN1 [ 5 Vdc ]
I/O Expander Port [ I2C ]
Analog Input Terminal [ Selectable ANA Input Type ]
Regulator [ 3.3 Vdc ]
FLASH
RESET
Power Input Terminal VIN2 [ 5 Vdc ]
I2C Input Terminal [2 PIN]
R-pull up
Handy sense board version 1.0
Handy sense bouad version 1.0 include of 4 part.
Part 1 Controller
Part 2 Actuator
Part 3 PIN input sensor
Part 4 SW and time ic
Part 1 is Controller part such as esp32, part 2 is actuator us relay trigger, part 3 is PIN input sensor value
such as analog and i2c and final part is RTC1307 time-ic and sw for reset and sw other controls.

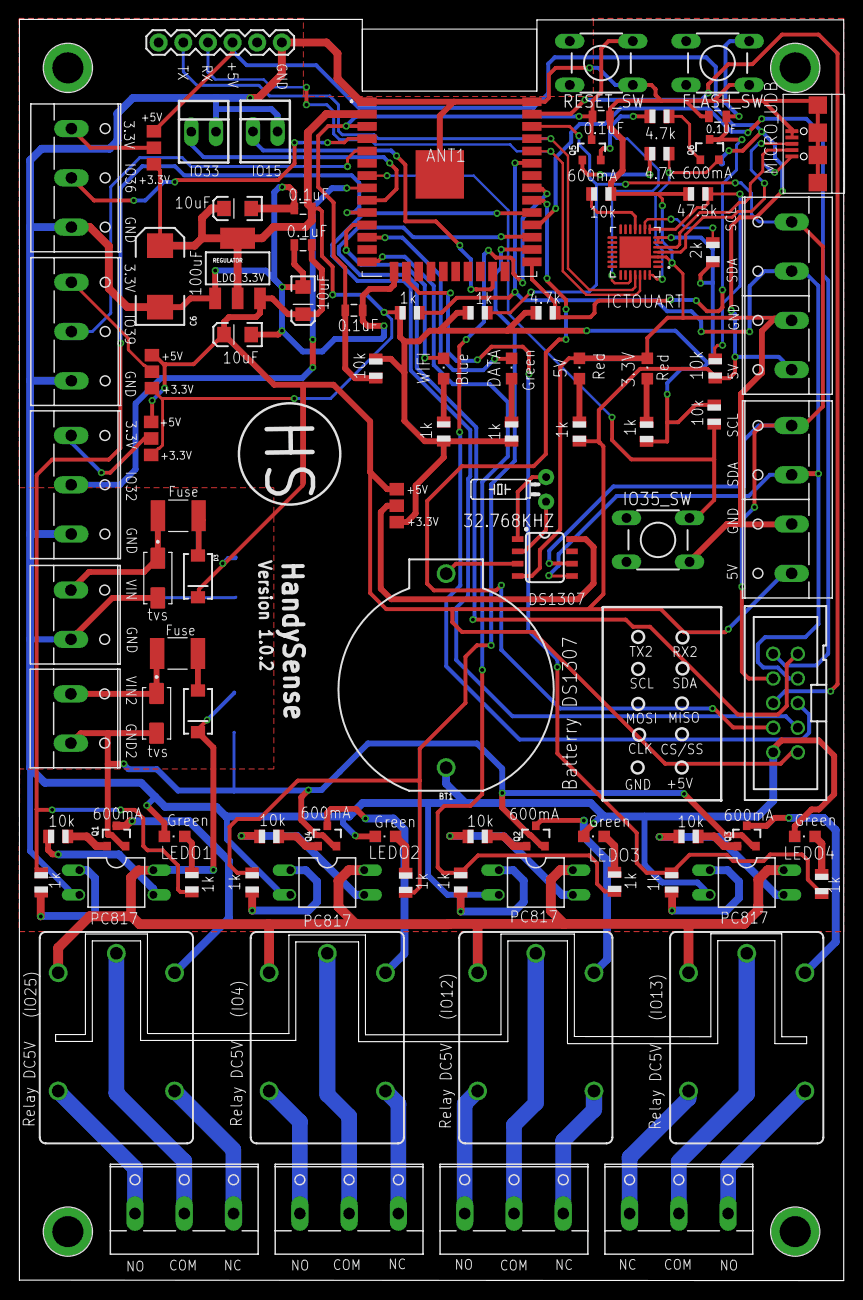
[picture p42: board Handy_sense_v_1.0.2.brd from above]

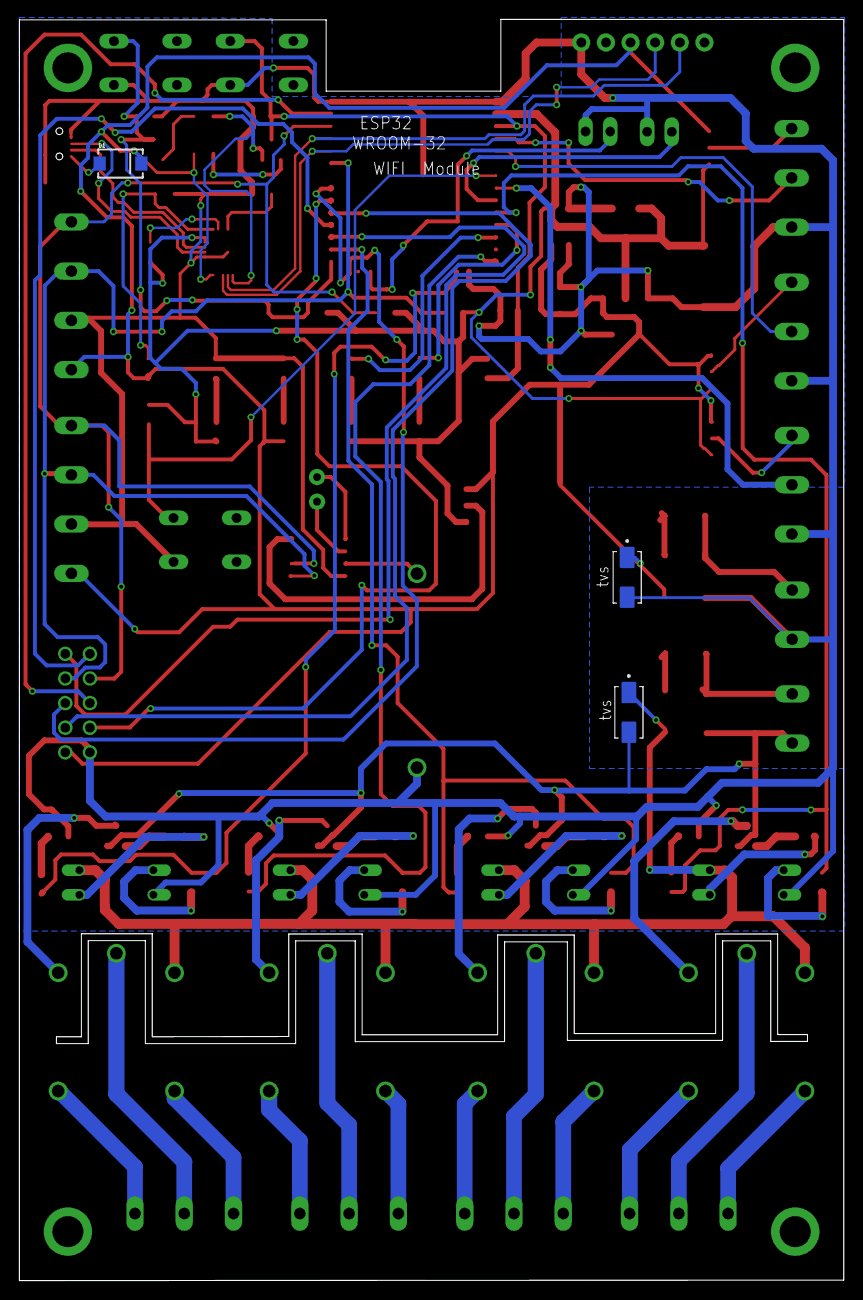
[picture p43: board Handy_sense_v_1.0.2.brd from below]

Board: 2 copper layers, 85.0 x 130.1 mm, 100 parts (3 on the bottom side), 86 nets.

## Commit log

2021-03-19 HandySense Version 1.0
    include
    - ฺBluePrint, schematic, PCB layout
    - BOM
    - Firmware
    - Dashboard
    - How to use
    [HandySense_v1_DOM.ods]
2021-03-24 rename HandySense
    [HandySense_v1_DOM.ods]
2021-04-19 ีupdate BOM
    [HandySense_v1_DOM.ods]
2021-05-12 ีUpdate doc
2021-06-25 update BOM
    [HandySense_v1_BOM.ods]
2021-09-16 new version 1.0.2
    [HandySense_v1.0.2_BOM.ods, Handy_sense_v1_BOM.ods, Handy_sense_v_1.0.2.brd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]

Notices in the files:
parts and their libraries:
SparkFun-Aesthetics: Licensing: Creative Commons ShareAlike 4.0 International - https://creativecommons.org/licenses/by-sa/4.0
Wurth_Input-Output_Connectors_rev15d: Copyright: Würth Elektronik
